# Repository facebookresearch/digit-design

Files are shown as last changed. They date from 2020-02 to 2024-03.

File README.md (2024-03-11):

# DIGIT-DESIGN


<a href="https://digit.ml/">
DIGIT-logo
</a>

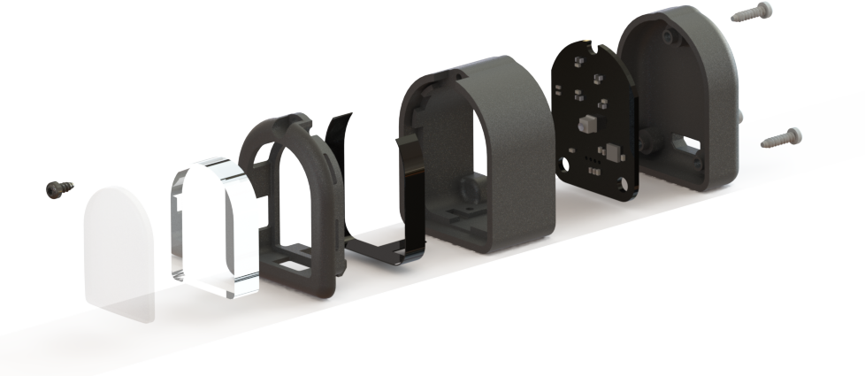
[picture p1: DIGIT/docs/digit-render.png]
DIGIT-render


Manufacturing design files for the [DIGIT tactile sensor](https://digit.ml).

**For updates and discussions please join the #DIGIT channel at the [www.touch-sensing.org](https://www.touch-sensing.org/) community.**

## Content

[This repository](DIGIT) contains the documentation and manufacturing files for the plastics enclosure, elastomer, electronics and the firmware binary.

## Design Notes

Due to some parts being out of stock due to shortages, we recommend the following part substituions:

* Digit Main PCB, Camera, OVM7692-RAAA with OVM7692-RYAA
* Digit Main PCB, MCU, FT900-R with FT900Q-C-T
* Digit Flex PCB, LEDs, ARGB1313HS-TR with 19-337C/RSBHGHC-A88/4T
    * Note: this change is only compatible with Digit Flex rev. 2021-2

## Quick Start

Manufacturing and assembly documentation is found in the [Quick Start Guide](/DIGIT/DIGIT_Quick_Start_Guide.pdf)

The manufacturing files are released in [releases](/DIGIT/releases) for PCBA fabrication.

## Questions and Contributing

If you have questions or need help with the content of this repo please open a ticket.
We welcome useful contributions to the repo -- if you want to contribute please read [how to contribute](CONTRIBUTING.md).

## License
These design files are licensed under CC-by-NC, as found in the [LICENSE](LICENSE) file.

## Citing
If you use this project in your research, please cite this [paper](https://arxiv.org/abs/2005.14679):

```BibTeX
@Article{Lambeta2020DIGIT,
  author  = {Lambeta, Mike and Chou, Po-Wei and Tian, Stephen and Yang, Brian and Maloon, Benjamin and Victoria Rose Most and Stroud, Dave and Santos, Raymond and Byagowi, Ahmad and Kammerer, Gregg and Jayaraman, Dinesh and Calandra, Roberto},
  title   = {{DIGIT}: A Novel Design for a Low-Cost Compact High-Resolution Tactile Sensor with Application to In-Hand Manipulation},
  journal = {IEEE Robotics and Automation Letters (RA-L)},
  year    = {2020},
  volume  = {5},
  number  = {3},
  pages   = {3838--3845},
  doi     = {10.1109/LRA.2020.2977257},
}
```
# DIGIT-PINKI-DESIGN



## Content

[This repository](DIGIT_Pinki) contains the documentation and manufacturing files for the plastics enclosure, elastomer, and assembly.

## Quick Start

Manufacturing and assembly documentation is found in the [Quick Start Guide](DIGIT_Pinki/DIGIT_Pinki_Quick_Start_Guide.pdf)

## Questions and Contributing

If you have questions or need help with the content of this repo please open a ticket.
We welcome useful contributions to the repo -- if you want to contribute please read [how to contribute](CONTRIBUTING.md).

## License
These design files are licensed under CC-by-NC, as found in the [LICENSE](LICENSE) file.

## Citing
If you use this project in your research, please cite this [paper](https://arxiv.org/abs/2403.05500).

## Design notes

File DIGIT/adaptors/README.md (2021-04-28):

DIGIT is designed to be natively compatible with the [Wonik's Allegro Hand](http://wiki.wonikrobotics.com/AllegroHandWiki/index.php/Allegro_Hand) 

In addition, we here provide files for 3d-printing adaptors for mounting DIGIT on several common robotic platforms:
- [Interbotix WidowX](https://www.trossenrobotics.com/widowxrobotarm)
- [Robotiq (2 and 3 fingers grippers)](https://robotiq.com/products)
- [Rethink Sawyer](https://www.rethinkrobotics.com/sawyer/)
- [Shunk](https://schunk.com/us_en/gripping-systems/category/gripping-systems/schunk-grippers/)
- [Weiss WSG Series](https://weiss-robotics.com/wsg-series/product/wsg-series/)

We welcome adaptors contributed from the community.

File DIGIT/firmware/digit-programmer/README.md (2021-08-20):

# DIGIT Programmer

A tool to allow flashing new firmware to the DIGIT device

This utility allows for downgrading or upgrading firmware, as well assigning a device serial number.

## Installation
Clone the repository and install the package using:

	git clone https://github.com/facebookresearch/digit-design.git
	cd digit-design/firmware/digit-programmer
	pip install -r requirements.txt

This tool also requires ```dfu-util```, install with:

    $ sudo apt install dfu-util

### Adding DIGIT and DIGIT-PROGRAM udev Rule
Add your user to the ```plugdev``` group,

    adduser username plugdev

Copy udev rule,

    sudo cp ./udev/50-DIGIT*.rules /lib/udev/rules.d/

Reload rules,

    sudo udevadm control --reload
    sudo udevadm trigger
    
Replug the DIGIT device into host.

### Firmware Download
The current public firmware release is found in the ```digit-design``` respository. 

## Usage
To upload firmware to the DIGIT device specify the path to the binary firmware file and the device's serial number (trailing zeros and D prefix is not required).

Default firmware binary file name is specified in ```programmer.yaml```.

Flashing DIGIT device with serial number ```D00045```,

    $ python3 flash.py digit.serial=45

Flashing DIGIT device with alternate firmware binary,

    $ python3 flash.py digit.firmware="digit-development.bin" digit.serial=45

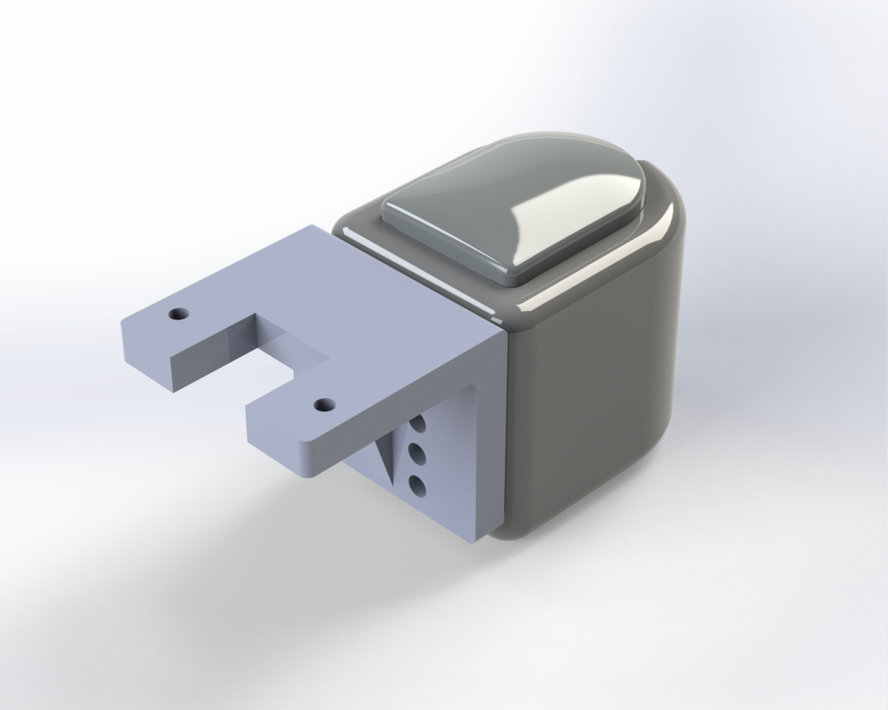
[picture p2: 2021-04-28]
DIGIT/adaptors/Interbotix/adaptor-interbotix.png

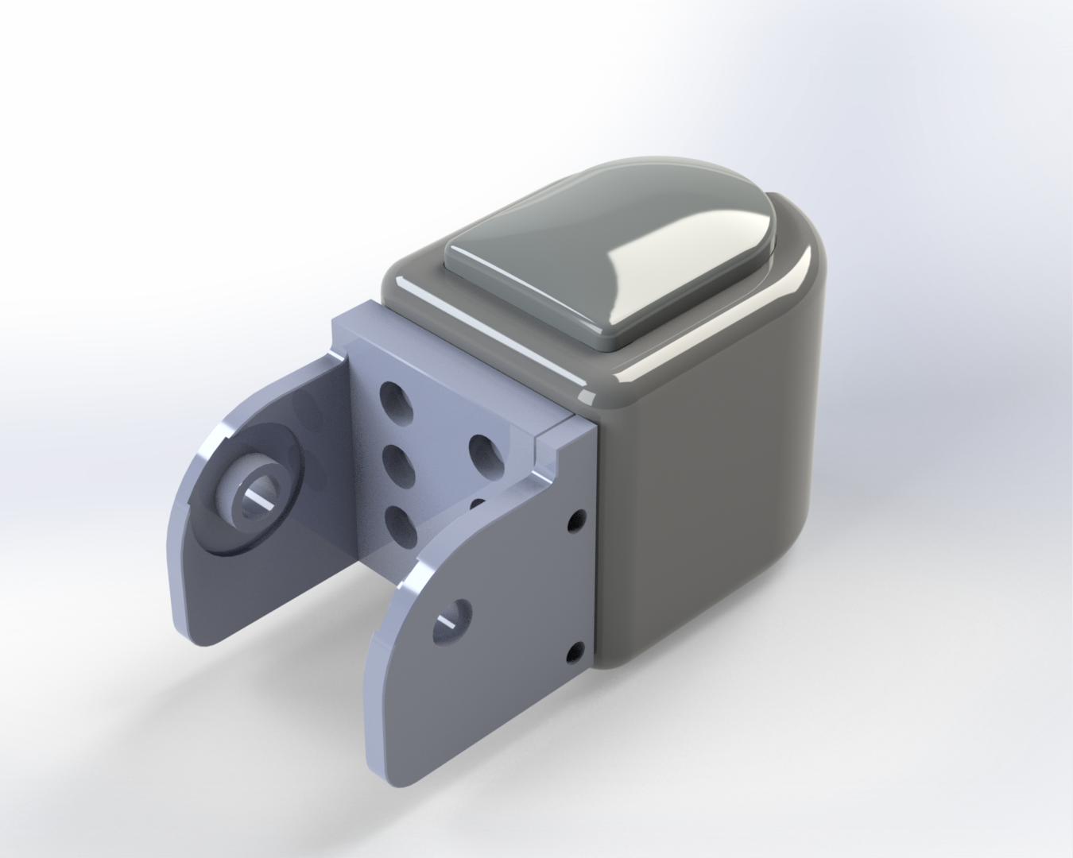
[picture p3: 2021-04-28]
DIGIT/adaptors/Allegro/adaptor-allegro.png

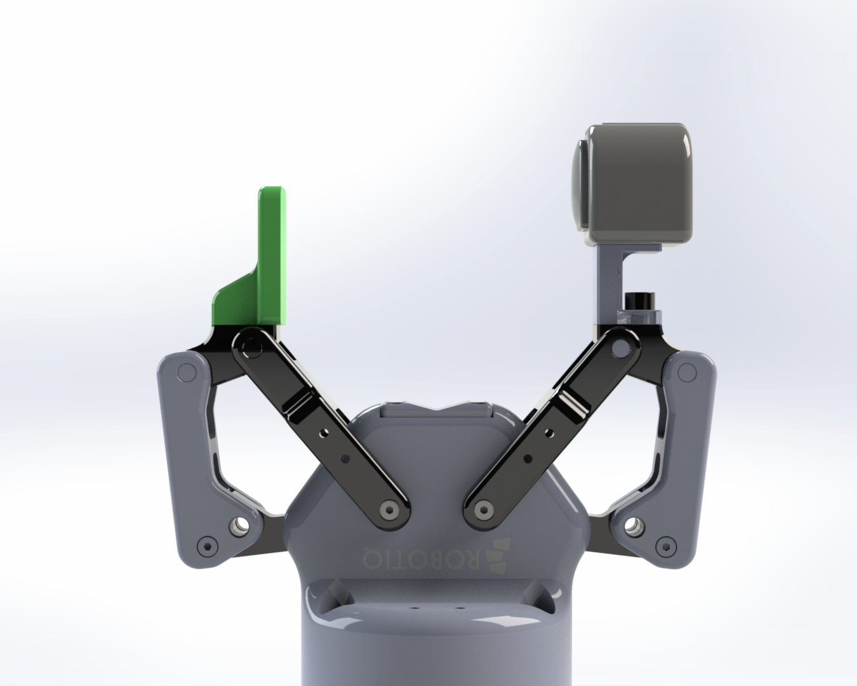
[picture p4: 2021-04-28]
DIGIT/adaptors/Robotiq/2F85/adaptor-robotiq-2f85.png

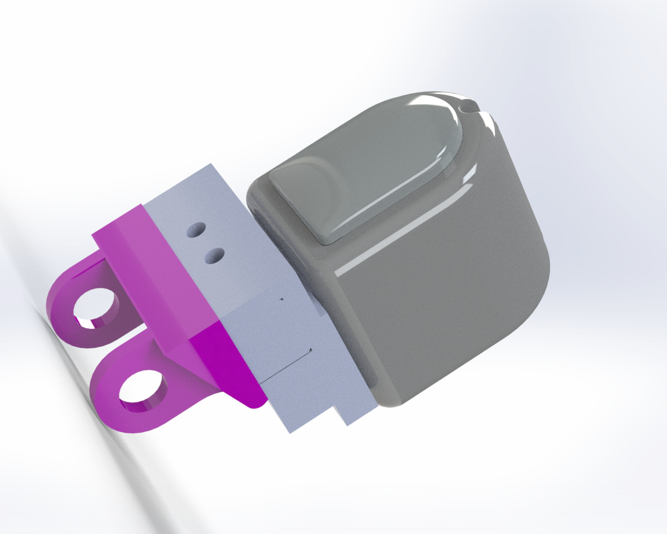
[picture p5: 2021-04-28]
DIGIT/adaptors/Robotiq/3-Finger/adaptor-robotiq-3-finger.png

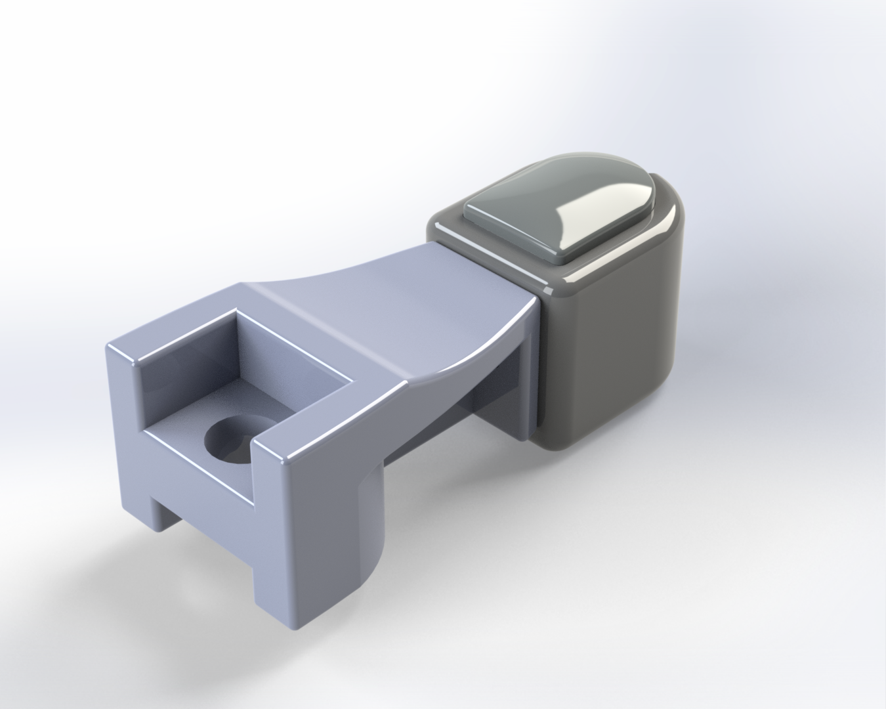
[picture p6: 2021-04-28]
DIGIT/adaptors/Schunk/adaptor-schunk.png

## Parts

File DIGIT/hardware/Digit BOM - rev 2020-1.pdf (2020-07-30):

Line # | Designator | Description | Qty. | Manufacturer | Manufacturer Part Number
1 | C1, C3, C4, C6, C7, C8, C10, C11, C12, C13, C17, C19, C21, C22, C23, C25, C26 | CAP 100nF 35V ±20% 0402 (1005 Metric) Thickness 0.6mm SMD | 17 | TDK | C1005X7R1V104M
2 | C2, C5 | CAP 10uF 6.3V ±20% 0402 (1005 Metric) Thickness 0.6mm SMD | 2 | TDK | C1005X5R0J106M050BC
3 | C9, C24 | CAP 4.7uF 10V ±10% 0603 (1608 Metric) Thickness 0.55mm SMD | 2 | KEMET | C0603C475K8PACTU
4 | C14, C15 | CAP 18pF 10V ±10% 0402 (1005 Metric) Thickness 0.6mm SMD | 2 | Vishay Vitramon | VJ0402A180KXQCW1BC
5 | C16, C18, C20, C27, C28, C29, C30 | CAP 1uF 6.3V ±10% 0402 (1005 Metric) Thickness 0.6mm SMD | 7 | Kyocera AVX | 04026D105KAT2A
6 J1 | | Micro USB Receptacle, Type B, SMT, Vertical, with Through-Hole Shell Stakes, -30 to 85 degC, 5-Pin SMD, RoHS, Tape and Reel | 1 | Global Connector Technology | USB3140-30-0230-1-C
7 L1, L2, L3 | | 3.3µH Shielded Multilayer Inductor 1.05A 250mOhm Max 0603 (1608 Metric) | 3 | Murata | LQM18PN3R3MGHD
8 P1 | | 16 Position Connector Receptacle, Center Strip Contacts Surface Mount Gold | 1 | Hirose | DF37NB-16DS-0.4V(51)
9 Q1, Q2 | | Dual General Purpose Transistors, NPN, 6-Pin SOT-563, Pb-Free, Tape and Reel | 2 | ON Semiconductor | BC847CDXV6T1G
10 | R1, R13, R14 | 1K 0.063W 5% 0402 (1005 Metric) SMD | 3 | Yageo | RC0402JR-071KL
11 R2, R3, R6 | | Chip Resistor, 10 KOhm, +/- 5%, 63 mW, -55 to 155 degC, 0402 (1005 Metric), RoHS, Tape and Reel | 3 | Rohm | MCR01MZPJ103
12 | R4, R5 | 12K 0.063W 1% 0402 (1005 Metric) SMD | 2 | Yageo | RC0402FR-0712KL
13 | R7 | 100R 0.063W 5% 0402 (1005 Metric) SMD | 1 | Vishay Dale | CRCW0402100RJNED
14 | R8, R10, R12 | 270R 0.063W 5% 0402 (1005 Metric) SMD | 3 | Panasonic | ERJ-2GEJ271X
15 | R9 | 82R 0.063W 5% 0402 (1005 Metric) SMD | 1 | Panasonic | ERJ-2GEJ820X
16 | R11 | 150R 0.063W 5% 0402 (1005 Metric) SMD | 1 | Vishay Dale | CRCW0402150RJNED
17 U1 | | FT900 Embedded Microcontroller, support both CAN Bus and Ethernet features, -40 to +85 degC, 100-Pin QFN, Pb-Free, Tape and Reel | 1 | FTDI | FT900Q-R
18 | U2 | CMOS with Processor Image Sensor 640H x 480V 1.75µm x 1.75µm | 1 | OmniVision Technologies | OVM7692-RAAA
19 | U3 | Linear Voltage Regulator IC 1 Output 300mA SOT-25 | 1 | Diodes Incorporated | AP7343-33W5-7
20 U4 | | Micropower 1.5V CMOS Voltage Regulator with Shutdown Control, 5-pin SOT-23, Pb-Free | 1 | TI National Semiconductor | LP3992IMFX-1.5/NOPB
21 X1 | | 12MHz ±25ppm Crystal 18pF 150 Ohms 4-SMD, No Lead | 1 | ECS International | ECS-120-18-36-AGM-TR
Line # | Designator | Description | Qty. | Manufacturer | Manufacturer Part Number
1 | D1, D2, D3, D4, D5 | LED RGB DIFFUSED SMD | 3 | Stanley Electric | ARGB1313HS-TR
2 | P1 | CONN HDR 16POS SMD GOLD | 1 | Hirose | DF37B-16DP-0.4V(53)

DIGIT Bill of Materials, Rev 2020-1

DIGIT Flex Bill of Materials, Rev 2020-1

Copyright (c) Facebook, Inc. and its affiliates. All rights reserved. This file is licensed under the license found in the LICENSE file in the root directory of this source tree.

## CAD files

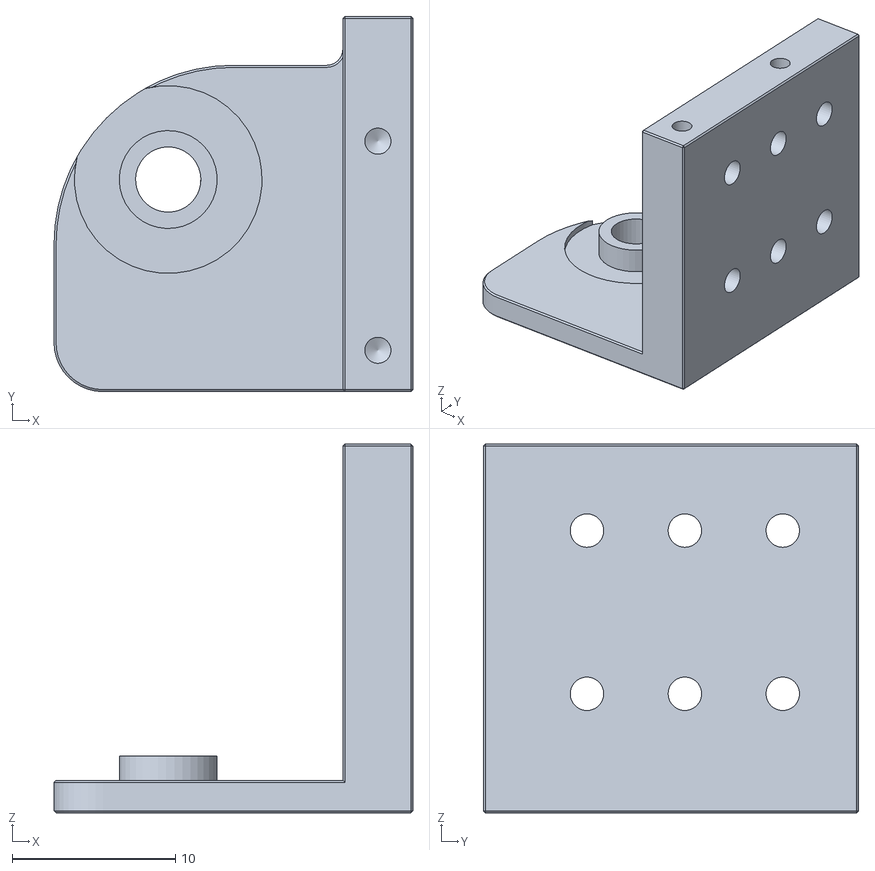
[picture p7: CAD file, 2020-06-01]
DIGIT/adaptors/Allegro/DIGIT-Allegro-main-V1.stl
22.0 x 23.0 x 22.6

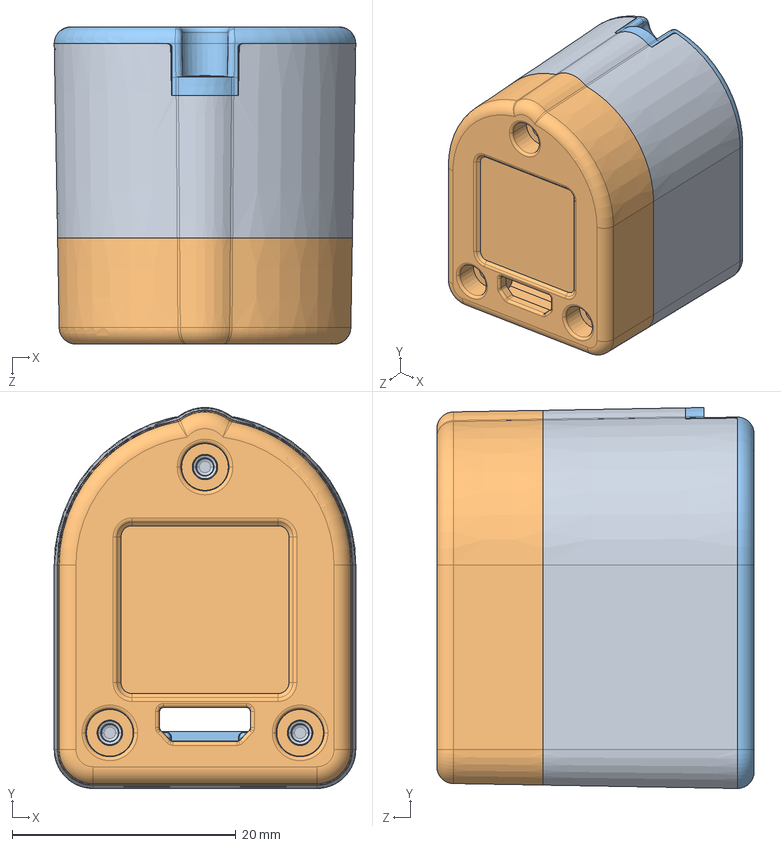
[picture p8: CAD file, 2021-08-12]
DIGIT/mechanical/EnclosureAssy_IM_Final.STEP
26.9 x 34.0 x 28.4 mm
CenterREDO_copy
BackREDO_copy
acrylicwindowREDO_rev2_copy

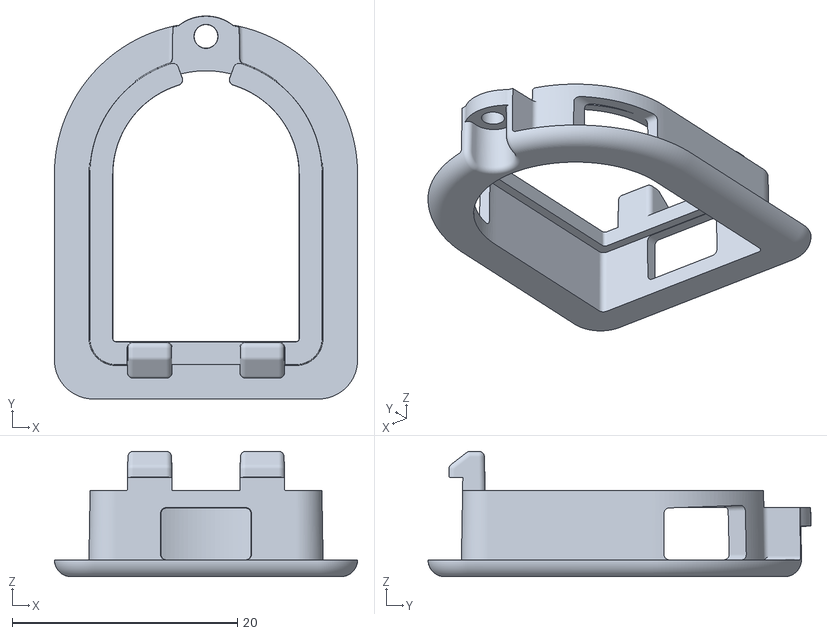
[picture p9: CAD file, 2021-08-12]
DIGIT/mechanical/EnclosureAssy_IM_Final_Window.STL
26.9 x 34.0 x 11.1

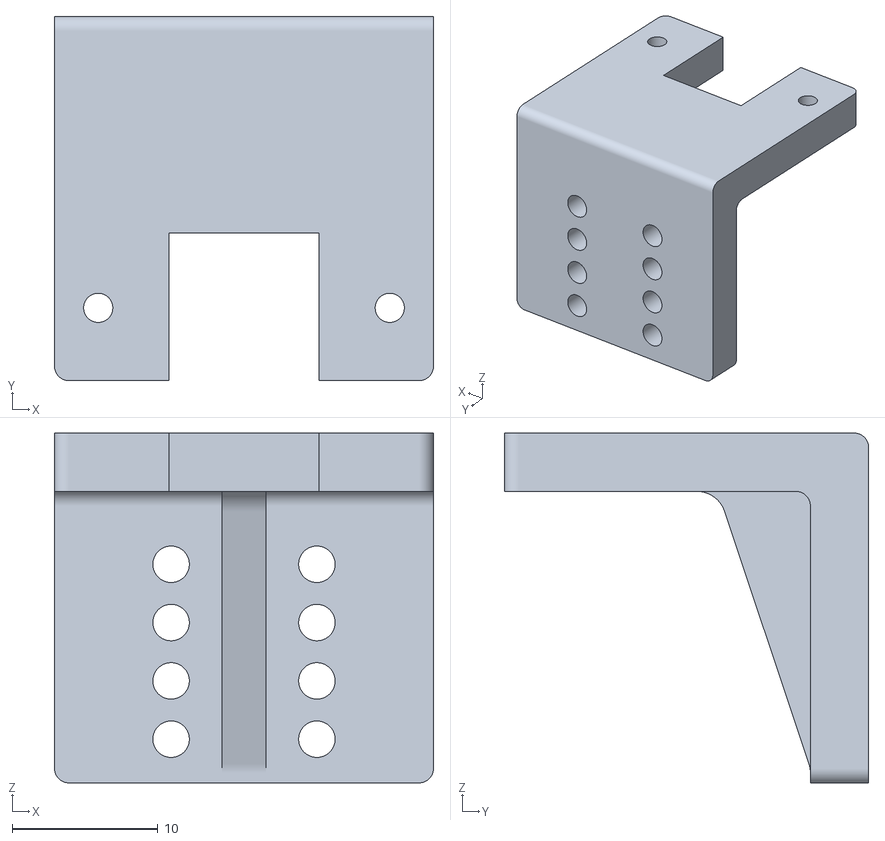
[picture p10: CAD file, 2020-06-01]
DIGIT/adaptors/Interbotix/DIGIT-WidowX-V1.STL
26.0 x 25.0 x 24.0

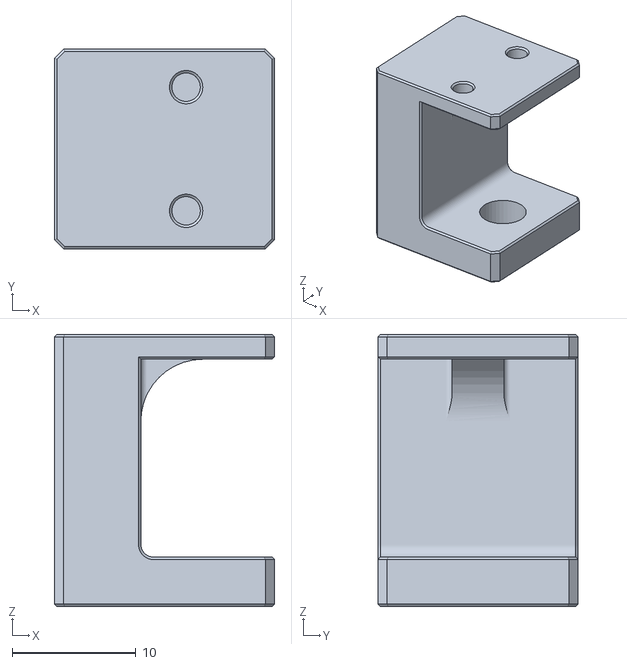
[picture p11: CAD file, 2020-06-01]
DIGIT/adaptors/Robotiq/2F85/DIGIT-Robotiq Adapter-2F85-V1.STL
17.8 x 16.2 x 22.0

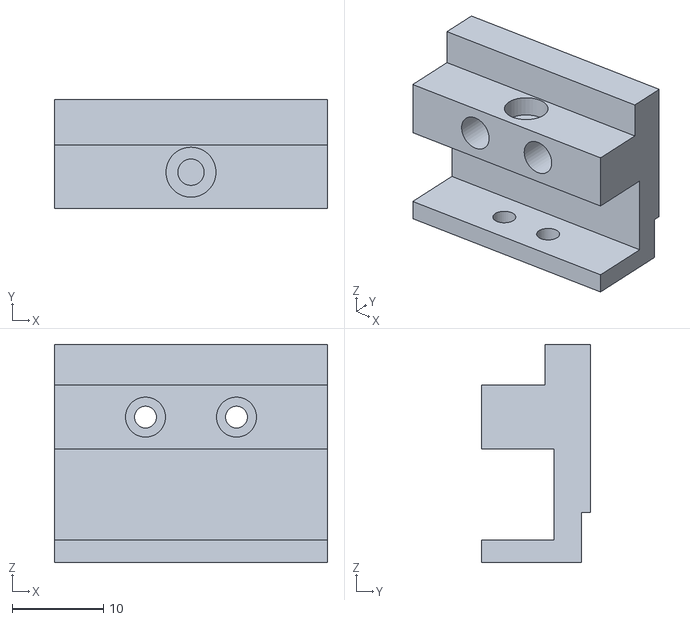
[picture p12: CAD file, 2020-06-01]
DIGIT/adaptors/Robotiq/3-Finger/DIGIT-robotiq-3fgr-bracket-V1.STL
30.0 x 12.0 x 24.0

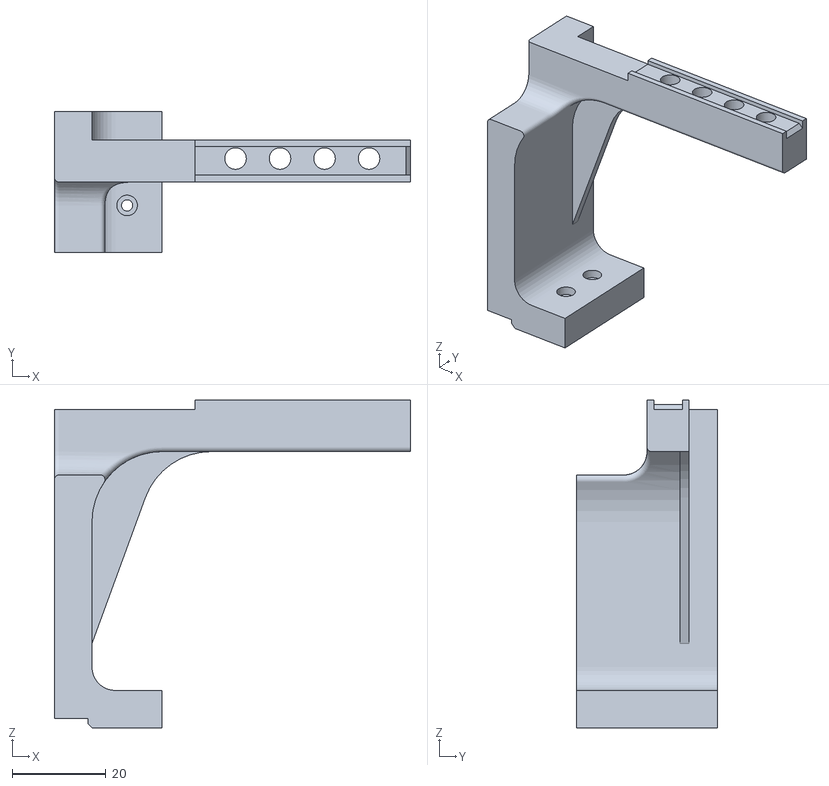
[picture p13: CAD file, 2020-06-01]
DIGIT/adaptors/Sawyer/DIGIT-Sawyer-V1.STL
76.0 x 30.0 x 70.0

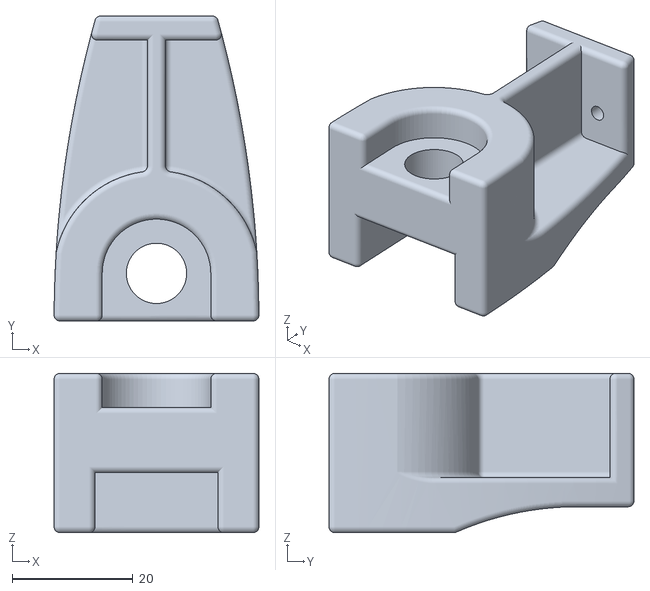
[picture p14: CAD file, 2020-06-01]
DIGIT/adaptors/Schunk/DIGIT-Schunk-V1.STL
34.0 x 50.6 x 26.5

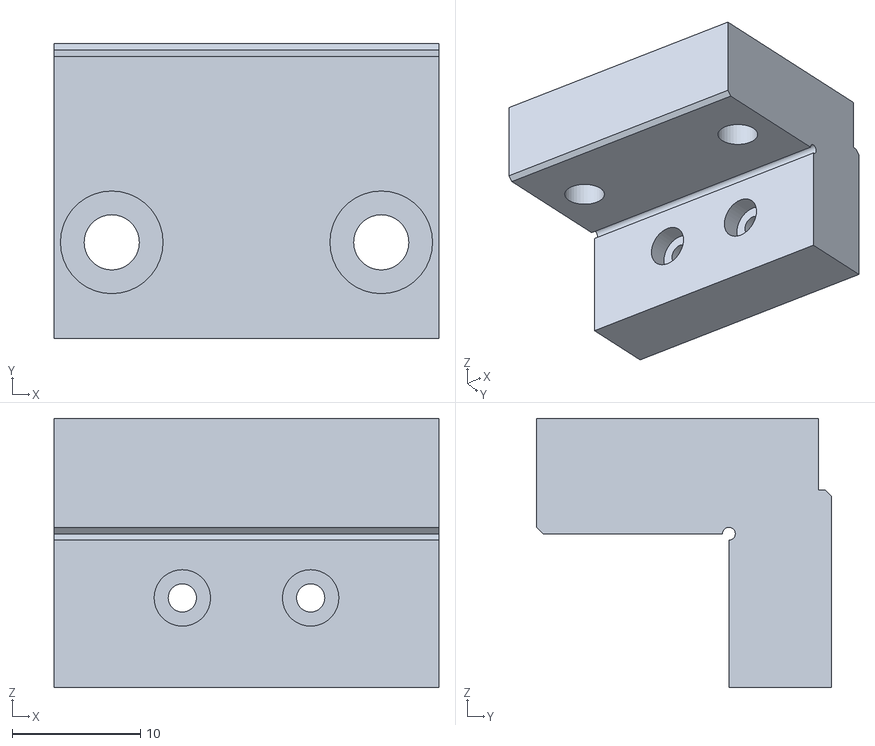
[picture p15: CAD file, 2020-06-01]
DIGIT/adaptors/Weiss/DIGIT-WSG-50-V1.STL
30.0 x 23.0 x 21.0

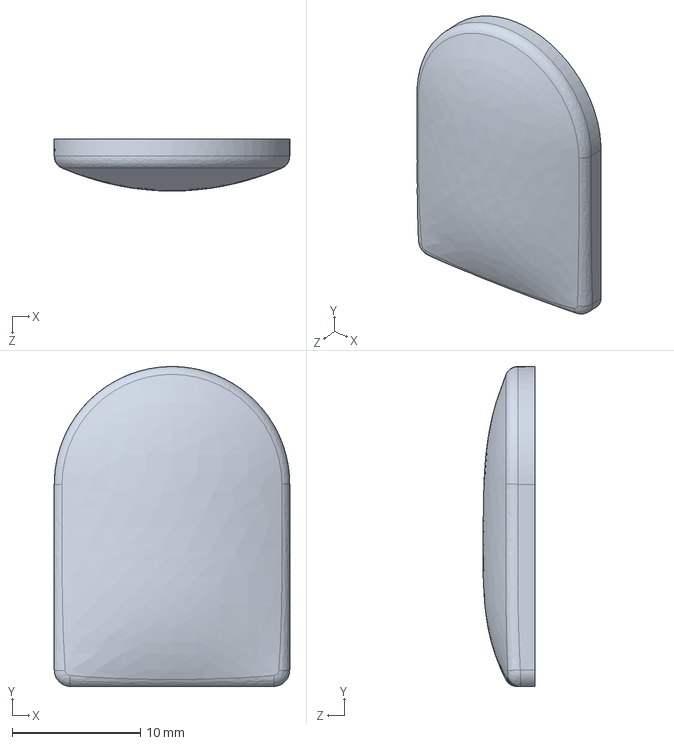
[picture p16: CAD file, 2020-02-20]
DIGIT/gel/Digit Gel.STEP
18.4 x 25.0 x 4.06 mm

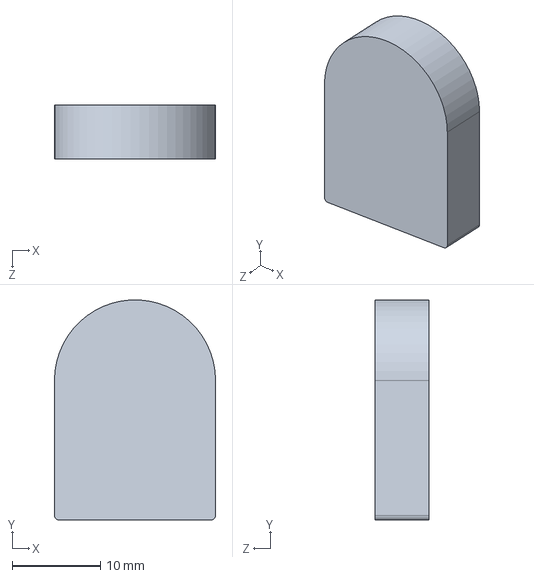
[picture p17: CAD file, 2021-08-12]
DIGIT/mechanical/Acrylic_Final.STEP
18.3 x 25.0 x 6.15 mm

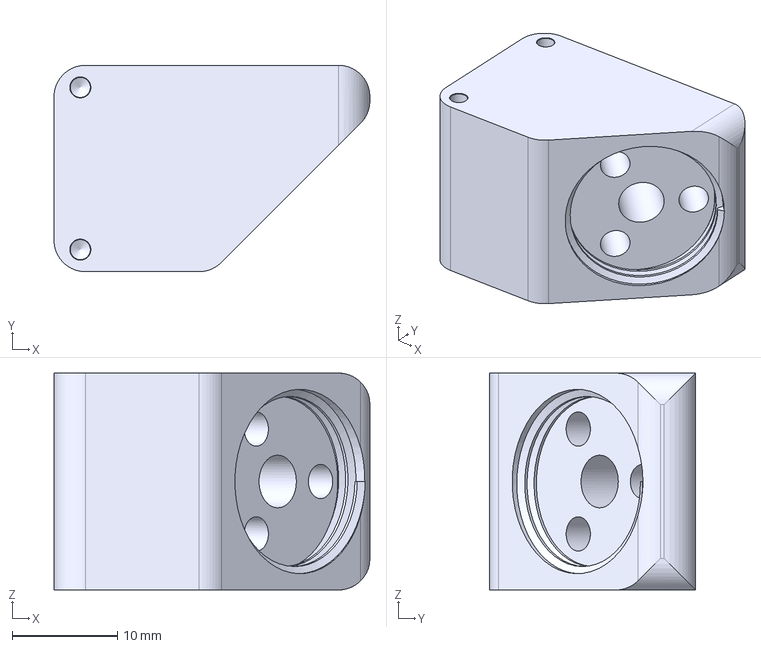
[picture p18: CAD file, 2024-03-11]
DIGIT_Pinki/adaptors/Allegro/AllegroHandAdaptor_3Fibers.step
30.0 x 19.6 x 20.6 mm

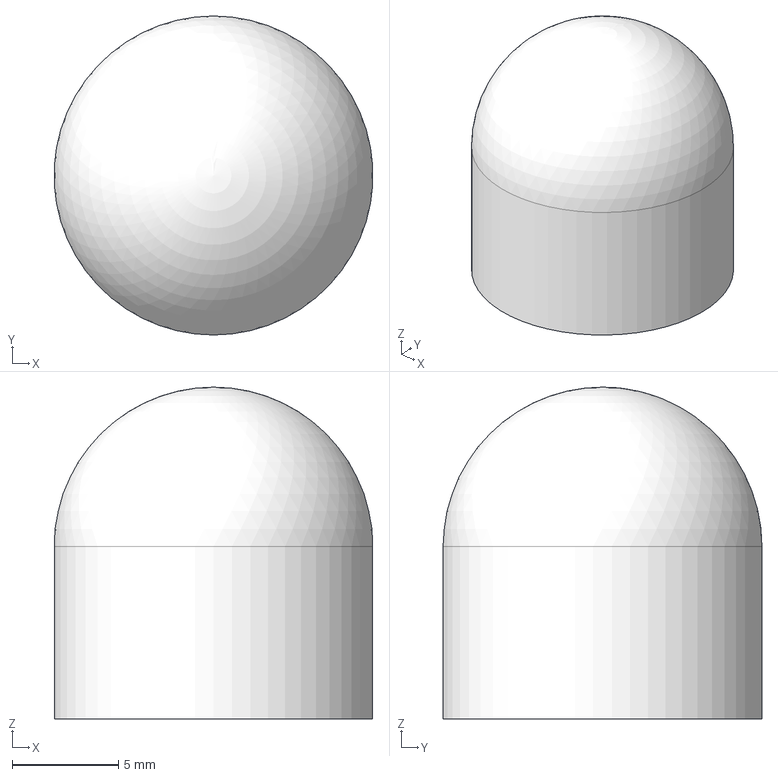
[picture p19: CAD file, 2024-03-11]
DIGIT_Pinki/gel/Pinki Gel.step
15.0 x 15.0 x 15.6 mm

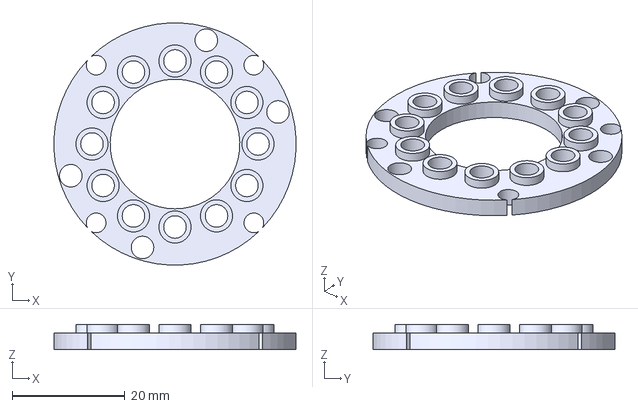
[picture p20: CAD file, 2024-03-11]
DIGIT_Pinki/mechanical/illumination/NeopixelLightGuideCollimator.step
42.9 x 42.9 x 4.50 mm

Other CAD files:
DIGIT_Pinki/mechanical/imaging/ArducamCageMount.step
DIGIT/adaptors/Allegro/DIGIT-Allegro-side-V1.stl
DIGIT/adaptors/Robotiq/3-Finger/DIGIT-robotiq-3fgr-base-V1.STL
DIGIT/mechanical/Label.DXF
DIGIT/mechanical/Acrylic_Final.DXF
DIGIT_Pinki/adaptors/Allegro/AllegroHandAdaptor_6Fibers.step
DIGIT_Pinki/adaptors/Allegro/AllegroHandAdaptor_9Fibers.step
DIGIT_Pinki/adaptors/Allegro/PinkiGelThread.step
DIGIT_Pinki/mechanical/illumination/NeopixelHolder.step
DIGIT_Pinki/mechanical/imaging/MicroscopeEyepieceCageMount.step

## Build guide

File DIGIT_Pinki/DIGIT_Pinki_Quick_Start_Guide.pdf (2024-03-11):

# DIGIT Pinki Quick Start Guide

# 1. Introduction

DIGIT Pinki is a compact, high-resolution tactile sensor suitable for operation in constrained spaces, such as medical palpation tasks. DIGIT Pinki uses optical fiber bundles to miniaturize the form factor of the sensing element significantly. This guide details the manufacturing, assembly, and quick start instructions for the DIGIT Pinki tactile sensor.

We recommend using the following printer settings for 3D-printed parts:

# 2. Distal Sensing Element Manufacturing

List of materials needed for making the elastomer gel and distal sensing element:

Part Number | Description | Quantity
1 | DIGIT Gel Mold | 1
2 | Vacuum degas chamber | 1
3 | Smooth-on Solaris Shore 10A | 1
4 | Smooth-on InhibitX | 1
5 | Smooth-on Ecoflex 00-10 | 1
6 | Smooth-on Silc-Pig White | 1
7 | Smooth-on NOVOCS Matte | 1
8 | Smooth-on Ease Release 200 | 1
Component | Specification
3D Printer | Stratasys J750
Layer Height | Default
Material | Vero Black Plus
Finish | Glossy

9 | Rustoleum Mirror Effect Spray | 1
10 | 99% Isopropyl Alcohol | 1
11 | Nitrile Glove | 2
12 | Cups | 2
13 | Wooden Mixing Sticks | 2
14 | Digital Scale | 1

To create the mold for the elastomer gel, one may either machine a metal mold or create a daughter mold. If you choose to machine the mold using the provided mold file (recommended), skip to Section 2.2. If you choose to create a daughter mold, go to Section 2.1.

## 2.1. Gel Daughter Mold

This section details how to create a daughter mold using silicone from a blank copy of the desired gel shape.

Materials needed in addition to the above material list:
- 1 pint unit of Mold Star 16
- 3D-printed or machined DIGIT Pinki gel shape
1. Clean the DIGIT Pinki gel shape with 99% isopropyl alcohol and place into a clean mold container, such as a cup or a box.
a. Use a silicone mold release on mold container if needed, letting outgas for 15-30 minutes after spraying.
b. Using mold release on the gel shape will create surface texture, so we recommend using a 3D-printed or machined gel shape.
2. Mix Mold Star 16 using 1:1 Part A to Part B by weight ratio, using the digital scale. After mixing well, pour mixture over the mold container until the Mold Star silicone fully encapsulates the gel shape.
3. Place in a vacuum degas chamber and vacuum 1 - 3 cycles at -85 kPA until there are no bubbles in the mold
4. De-mold the daughter mold from the container once Mold Star has cured after 4+ hours

## 2.2. Gel Base

This section details how to create the elastomer gel base once a mold (either machined or silicone) has been obtained.

Optional Materials:
- (Optional) Syringes with Luer Lock tip (recommended 14 Ga size or larger)
- (Optional) KimTech wipes
1. Clean the mold with 99% isopropyl alcohol and let the alcohol dry off.
2. (Only if you are using a silicone daughter mold) Spray the mold with silicone mold release, holding the mold release spray at least 6 inches away for an even coating.
a. Let outgas for 15-30 minutes
b. If there is too much excess mold release, repeat steps 1 and 2 again to avoid unnecessary surface texture.
3. Using a cup and wooden mixing stick, mix Solaris using 1:1 Part A to Part B by weight ratio.
4. Place the mixture in a vacuum degas chamber and vacuum for 1-3 cycles at -85kPA until there are no bubbles in the Solaris
5. Pour the Solaris mixture into the mold cavity.
a. (Optional) For more precision when putting the Solaris into the mold, use a syringe with a 14 Ga size or larger Luer Lock tip. Below is an image of Solaris injected into a silicone mold cavity.

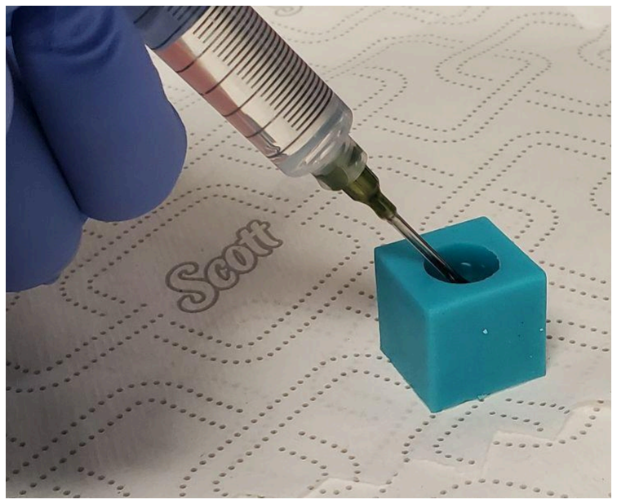
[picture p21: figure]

6. Place the filled mold into the vacuum degas chamber and again vacuum at 1-3 cycles at -85 kPA until there are no bubbles in the Solaris gel. This is to remove any bubbles that were introduced during the pouring process.
7. Let the Solaris cure for 24+ hours at room temperature and atmosphere pressure. We recommend covering the mold to prevent any dust
8. Demold the gel from the mold.

## 2.3. Gel White Paint Mixture

Next, prepare the white silicone paint mixture that will coat the finished gel surface.

1. Mix Smooth-on Ecoflex 00-10 evenly with equal parts A and B.
2. Add in 3% white Silc Pig pigment by weight.
3. Dilute the white Ecoflex 0010 with NOVOCS matte 0.8% by weight. The result should have a similar consistency to liquid yogurt. You may test out the mixture and add more or less NOVOCS matte as suitable.
4. Set aside the resulting white silicone paint mixture for the final assembly step.

## 2.4. Gel Surface Layer Assembly

This section details how to create the surface layers on top of the optically-clear base gel.

Optional Materials:
- (Optional) Airbrush system
- (Optional) heat gun
- (Optional) Latex-free cosmetic blender wedge
1. Clean surface of the Solaris gel with 99% isopropyl alcohol

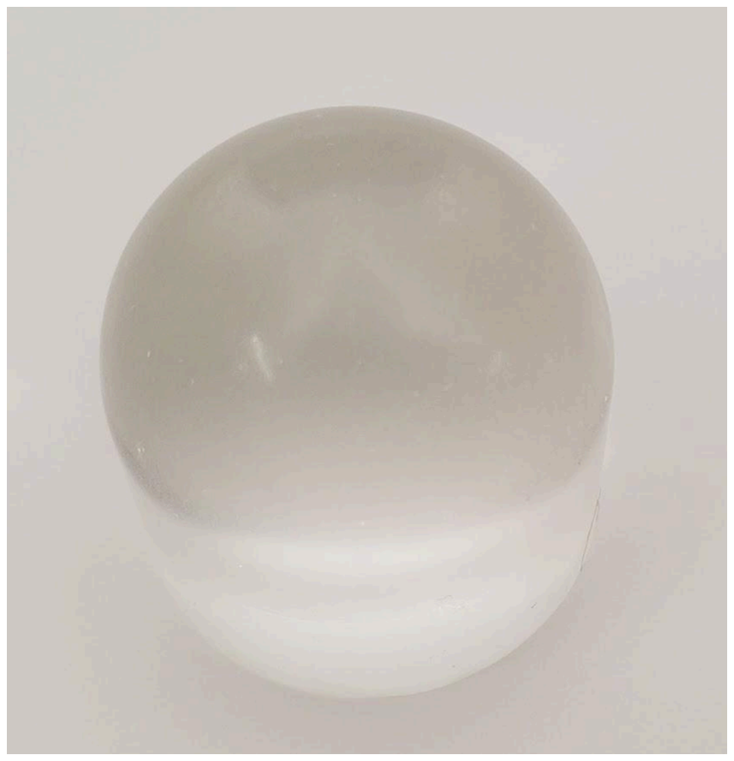
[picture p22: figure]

2. Coat the gel with a thin layer of InhibitX (may be airbrushed if desired).
a. Let outgas for 15 - 30 minutes.
3. Using Rustoleum Mirror Effect, spray the gel with 3-5 horizontal passes across the entire surface until there is an even silver coating.
a. Let dry for 15 - 30 minutes.
4. Apply another thin (may be airbrushed) layer of InhibitX
a. Let outgas for 15 - 30 minutes
5. Using a thin wooden mixing stick, thinly drip coat the surface of gel with the white paint silicone mixture. The mixture should drip down like coating a candy surface.

a. (Optional) Use a Latex-free cosmetic foam blender wedge or a syringe to evenly distribute the white silicone if dripping is not sufficient
b. Set aside in a covered (dust-free) environment to cure for 4 hours or set using heat gun if time sensitive.

## 2.5. Sensing Element Assembly

With a completed hemispherical gel (with the reflective layer and protective white paint layer), we may then assemble it into the mechanical enclosure.

Part Number | Description | Quantity
1 | 3D-printed thread | 1
2 | 3D-printed housing enclosure | 1
3 | Cyanoacrylate | 1
4 | Cargille Optical Gel | 1
1. Using cyanoacrylate, adhere the 3D-printed thread to the base of the gel so that the gel may be screwed onto the housing enclosure.
2. Use the index-matched Cargille optical gel on the base of the gel before screwing it on.

# 3. Illumination System Fiber Assembly

In this section, we detail how to assemble the illumination fiber bundle.

Part Number | Description | Quantity
1 | PMMA Fibers (e.g. 265μm with 48 Fiber Light Guide) | 1
2 | Razor blade or cutting knife | 1
3 | Sandpaper (180, 400, 1000 grit) | 1
4 | 99% Isopropyl Alcohol | 1
5 | Cyanoacrylate (super glue) | 1

6 | Sil-Poxy | 1
7 | Neopixel Ring | 1
8 | 3D-printed Neopixel Enclosure | 1
1. Cleave fiber ends using a razor blade. If possible, use a fiber cutting block or other similar jig in order to ensure a blunt, perpendicular face
2. Polish and clean fiber ends:
a. Use 180 grit (dry), 400 grit, and then 1000 grit (wet) sandpaper. Sand in a “Figure 8” motion for 20 passes with each sandpaper.
b. Clean the end faces with 99% isopropyl alcohol after sanding.
3. Bundle the fibers into the fiber mount.
4. Press fit the fiber bundle into fiber mount and use sharp scissors or shears to trim to edge.
a. Securely adhere using one drop of cyanoacrylate.
5. Adhere mount to elastomer gel through the enclosure conduits using Sil-Poxy
a. Do not move until Sil-Poxy has cured or else the mount will delaminate
6. On the illumination side, adhere fibers to LEDs using cyanoacrylate

# 4. Imaging Optical Bench Setup

In this section we describe the setup used for magnifying and imaging the output from the coherent fiber bundle.

List of materials needed:

Part Number | Description | Quantity
1 | Coherent Imaging Fiber Bundle with Adjustable Diopter | 1
2 | 16MP IMX298 USB camera | 1
3 | 10x plan Microscope objective | 1
4 | Microscope Eyepiece | 1
5 | ThorLabs Optical Metric Breadboard | 1
6 | ThorLabs Cage Plate Mounting Base for 30 mm Cage | 1

6 | ThorLabs 30 mm C-Mount-Threaded 30 mm Cage Plate | 1
7 | 3D-Printed Custom Cage Mount for Microscope Eyepiece | 1
8 | 3D-Printed Custom Cage Mount for Arducam | `1
9 | ThorLabs 30 mm Cage System Cover | 1
10 | ThorLabs 6 Inch Optical Cage Rods | 1
11 | 99% Isopropyl Alcohol | 1
12 | KimTech Wipes | 2
13 | M6 Screws | 4
14 | M4 Screws | 2
15 | (Optional) ThorLabs Cage Alignment Guide | 1
1. Assemble the optical cage and optical relays:
a. Align the 10x plan microscope objective and microscope eyepiece to the breadboard by screwing them into the C-mount cage plate and the custom 3D-printed cage plate, respectively.
b. Secure both to the optical cage to the breadboard using the metric screws
c. Attach the rods
d. Remove any dust using the KimTech wipes and 99% Isopropyl Alcohol.
2. (Optional) Verify alignment visually using the ThorLabs Cage Alignment Guide
3. Then align the USB camera to one end of the optical relays, and the coherent fiber bundle to the other end of the optical relays.
4. To verify the system, plug in the USB camera to your computer and verify that you can see the fibers clearly.
a. If the image is out of focus, manually focus the lens on the USB camera or the adjustable diopter.

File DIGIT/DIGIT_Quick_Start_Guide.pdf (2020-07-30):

# Quick Start Guide

[ 06 June 2020 ]

## 1 Introduction

DIGIT [1], is an inexpensive, compact, and high-resolution tactile sensor geared towards in-hand manipulation. DIGIT improves upon past vision-based tactile sensors by miniaturizing the form factor to be mountable on multi-fingered hands, and by providing several design improvements that result in an easier, more repeatable manufacturing process, and enhanced reliability. To provide the robotic community access to reliable and low-cost tactile sensors, we open-source the DIGIT design at www.digit.ml.
This white paper aims to provide manufacturing, assembly and quick start instructions for the DIGIT tactile sensor.

## 2 Repositories

There are two main repositories which contain the open-sourced sensor design, and a Python library for interfacing with the DIGIT sensor.
https://github.com/facebookresearch/digit-design
https://github.com/facebookresearch/digit-interface

1

## 3 Required Materials

### 3.1 Components List

DIGIT assembly requires the following tools and off-the-shelf components:

Part No. | Description | Quantity
1 | 1.5 mm Metric Hex Driver | 1
2 | Hex Socket Screw M2 x 0.4 mm Thread, 5 mm Long | 3
3 | Hex Socket Screw M2 x 0.4 mm Thread, 3 mm Long | 1

The following components compose the DIGIT main electrical and mechanical design, which are manufactured through internal or external vendors.

Part No. | Description | Quantity
1 | DIGIT Printed Circuit Board (PCB) | 1
2 | DIGIT Lighting PCB | 1
3 | DIGIT Rear Housing | 1
4 | DIGIT Main Housing | 1
5 | DIGIT Acrylic Clip Housing | 1
6 | Acrylic Window | 1
7 | Gel | 1

2

## 4 Manufacturing Recommendations

### 4.1 Electrical

Two components are required which can be manufactured via a turnkey printed circuit board assembly service, or by hand populating manufactured PCBs.

- Main PCB containing camera system
- Lighting flex PCB

The Gerber design files are found within the digit-design repository and are manufactured with the following specifications:

Specification
Layer Count | 4
Material | 370HR or FR4
Min Track/Spacing | 4mil/4mil
Thickness | 1.6mm
Solder Mask | Black
Silk Screen | Top and Bottom
Silk Screen Color | White
Surface Finish | ENIG
Via Process | Tented Via
Finished Copper | 1 oz.
(a) Main PCB specifications

Specification
Layer Count | 2
Material | Polymide Flex
Min Track/Spacing | 3mil/3mil
Thickness | 0.23mm
Solder Mask | Black
Silk Screen | Top
Silk Screen Color | White
Surface Finish | ENIG
Via Process | Tented Via
Finished Copper | 1.5 oz.
(b) Flex PCB specifications

The PCB stackup for the 4 layer main PCB board is as follows,

- Top Layer - digit copper signal top.gtl
- Internal Layer 1 - digit copper signal 1.g1
- Internal Layer 2 - digit copper signal 2.g2
- Bottom Layer - digit copper signal bot.gbl

3

### 4.2 Mechanical

The DIGIT mechanical body consists of three 3D-printed parts and one laser cut part. The 3D printed parts are the main, back, and acrylic clip housings shown in figure 1.

(a) Rear | (b) Main | (c) Acrylic Holder

Figure 1: Mechanical housing components

We recommend using the following 3D printer specifications,

Specification
3D Printer | Stratasys J750
Layer Height | Default
Material | Vero Black Plus
Finish | Glossy

Additionally, the gel acrylic window is laser cut from a sheet of 4 mm thick optically clear acrylic.

4

## 5 Assembly

Upon manufacturing both the mechanical and electrical parts, DIGIT can be assembled within 5 minutes.

Step 1

Press fit the DIGIT PCB into the back housing as shown in figure.x.

Figure 2: PCB inserted into back housing

Step 2

Bend the flex PCB connector 90 degrees and insert the DIGIT flex PCB into the perimeter of the main housing as shown in Figure 3.

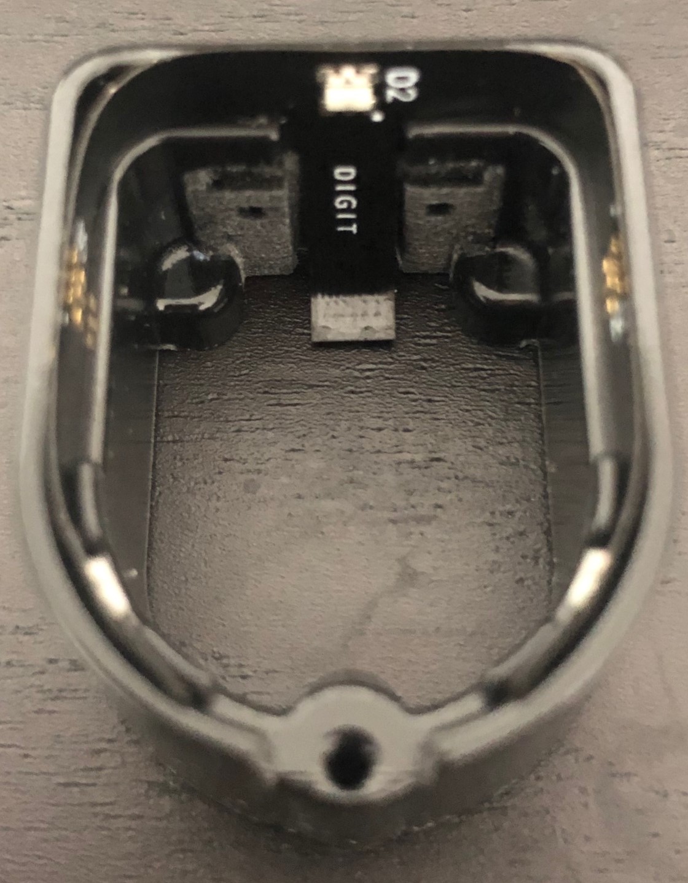
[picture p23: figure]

Figure 3: Flex PCB inserted into main housing

5

Step 3

Press fit the back and main housings together,

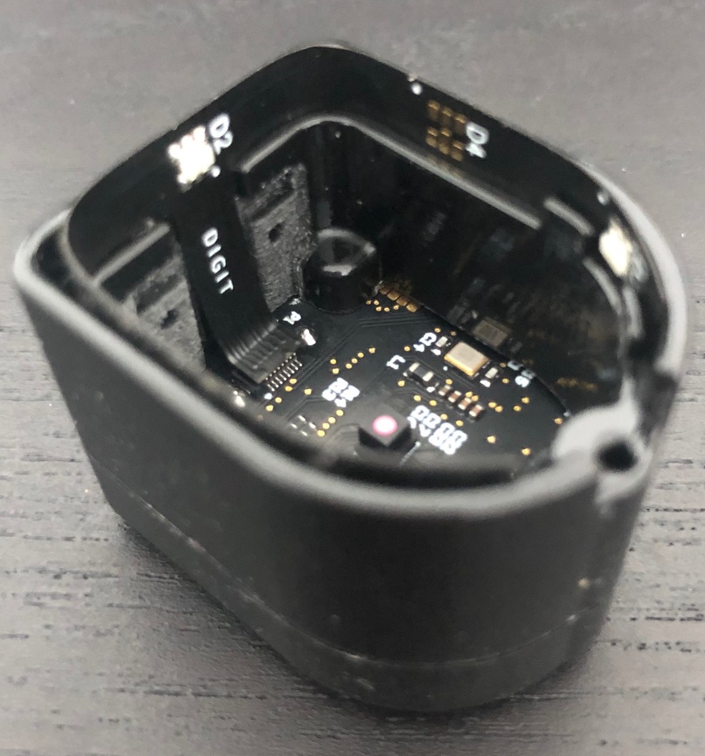
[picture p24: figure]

Figure 4: Back and main housing coupled together

Using your finger connect the flex PCB to the main PCB with a firm push, you should feel the connector snapping into place.

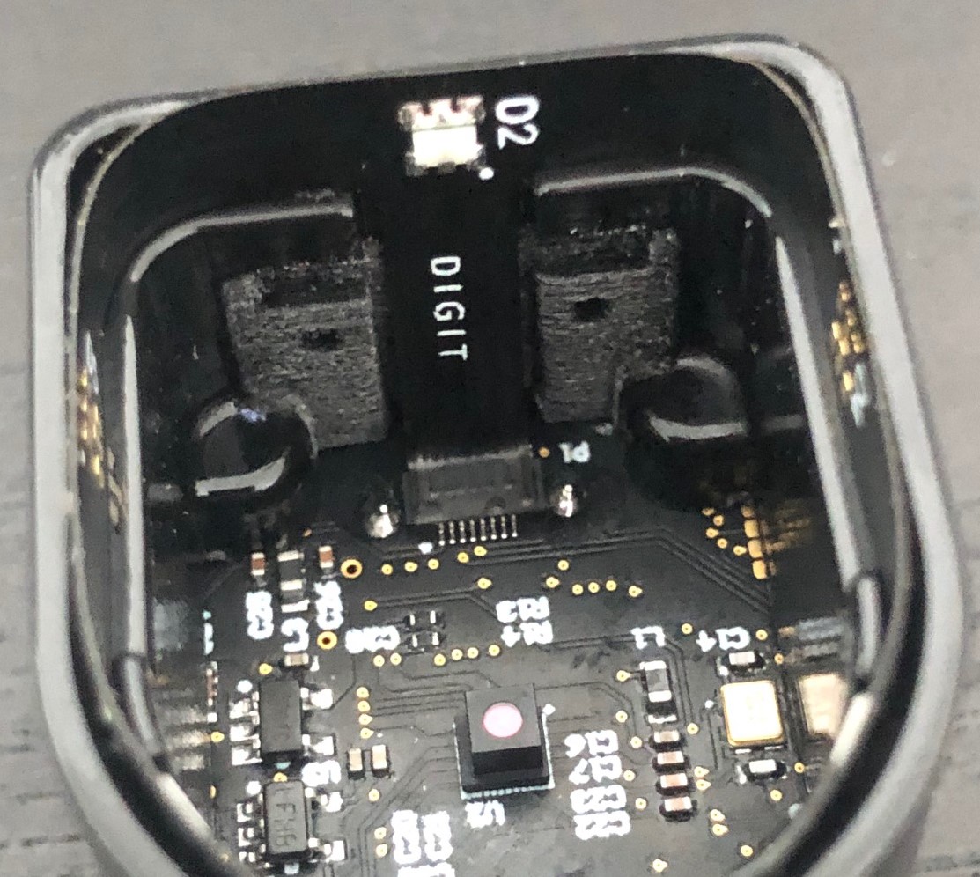
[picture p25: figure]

Figure 5: Flex PCB connected to main PCB

Step 4

Insert the gel into the acrylic holder housing,

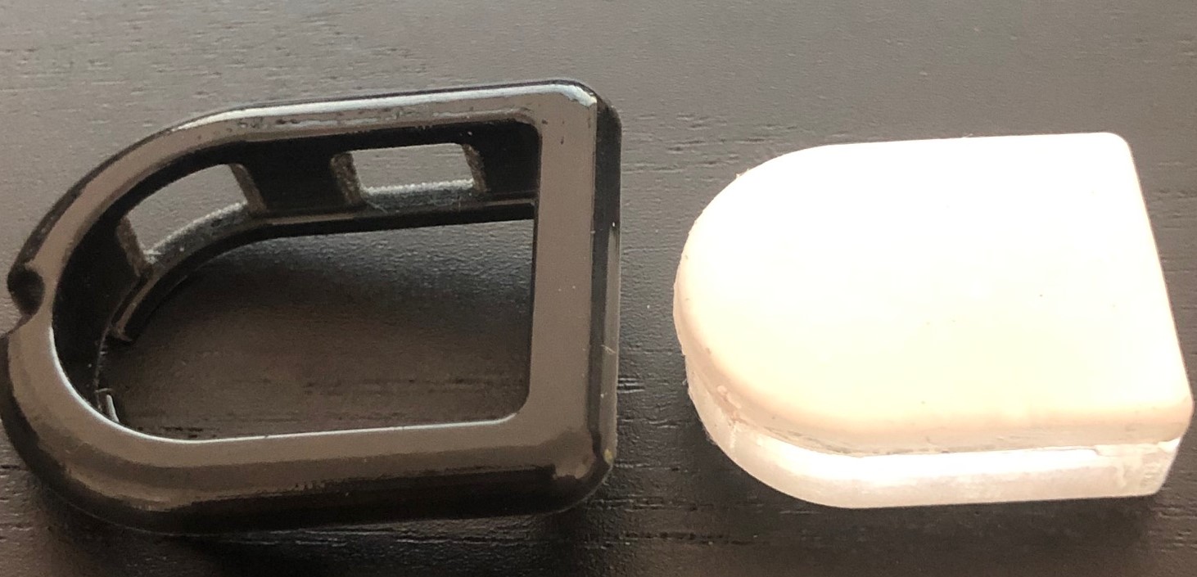
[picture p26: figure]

Figure 6: Gel and acrylic holder housing

Following this, snap fit the acrylic holder to the main housing,

6

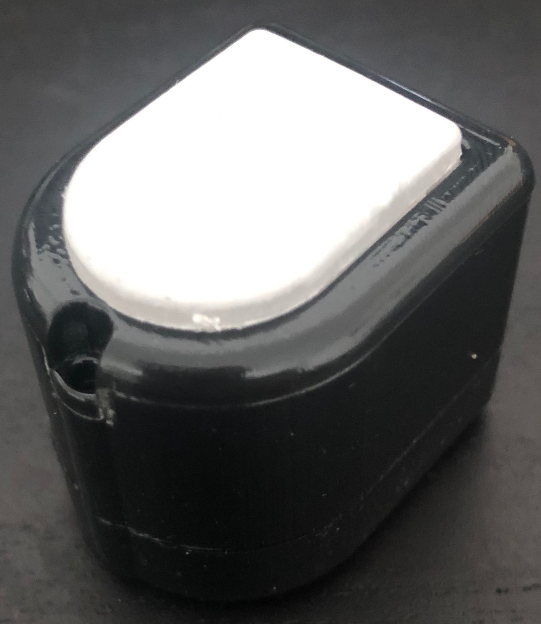
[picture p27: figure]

Figure 7: Main housing with acrylic housing

Step 5

Insert and fasten the three 5 mm hex screws into the back housing,

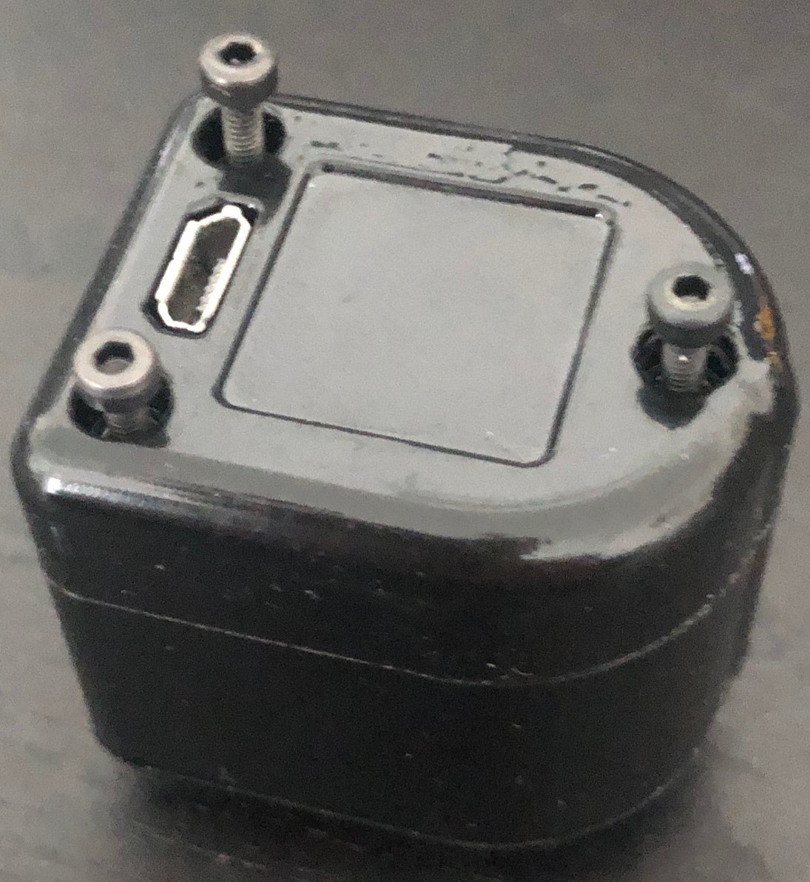
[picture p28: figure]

Figure 8: Back housing with inserted screws

Insert and fasten one 3mm hex screw into the acrylic housing,

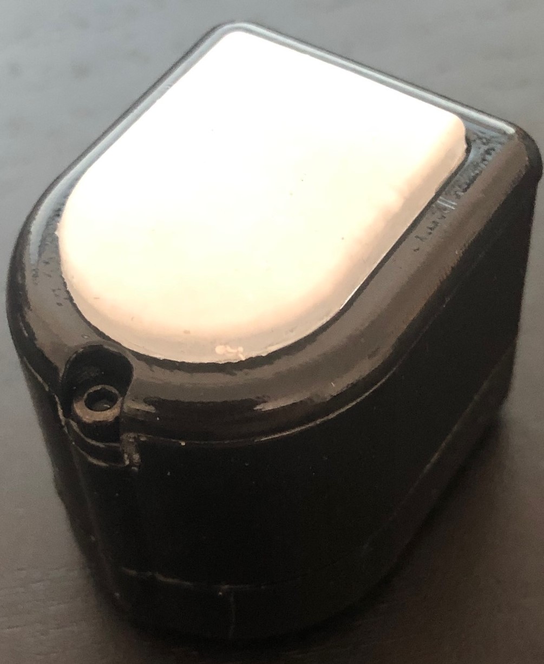
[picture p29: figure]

Figure 9: Acrylic housing with inserted screw

7

## 6 Gel Manufacturing

The DIGIT design repository contains the 3D files for the gel mold. This mold can either be produced via subtractive or additive manufacturing. The DIGIT gel mold consists of a 3x3 array of gels, it is best recommended to machine this mold out of aluminum. If manufacturing by 3D printing, sand each gel well in post to remove any layer lines.
It is recommended to start out with a small batch until all mixtures and results achieve the desired results for the end application. Following this, a large set of DIGIT gels can be produced by increase the number of molds and running larger batches.
The following tools, parts and chemicals are required for the manufacture of DIGIT gels.
Part No. | Description | Quantity
1 | DIGIT Gel Mold (gel/Digit Gel Mold.stp) | 1
2 | 2 x Airbrush Systems or 1 System with 2 Heads | 1
3 | Heat Source (Heat Gun or Blowdryer) | 1
4 | Smooth-On Solaris Shore 10A | 1
5 | Smooth-On Inhibit X | 1
6 | Smooth-On EcoFlex 00-10 | 1
7 | Smooth-On White Silicone Pigment | 1
8 | Smooth-On Sil-Poxy Optically Clear Adhesive | 1
9 | Smooth-On NOVOCS Matte | 1
10 | 99% Isopropyl Alcohol | 1

### 6.1 Preparing White Paint Mixture

Step 1

Mix an equal part A/B solution of EcoFlex 00-10.

Step 2

Add the white silicone pigment such that it is 3% of the total weight of the previous mixture.

Step 3

Thin out the mixture to 20% of the total weight using NOVACS and mix well until smooth. You may test out the mixture by observing how well the it is applied via the airbrush. Increase the amount of NOVACS until a uniform stream of white paint is expelled from the airbrush against a surface.

8

### 6.2 Manufacturing the DIGIT Gel

Step 1

Clean the molds thoroughly with 99% isopropyl alcohol and let dry.

Step 2

Apply Solaris 10A silicone into the molds and let cure on a flat surface, and inside a contained space with no turbulent air movement.

Step 3

Remove the gels from the mold and clean with 99% isopropyl alcohol.

Step 4

Arrange the gels on a flat plastic (sheet of acrylic) surface with the curved surfaces facing upwards.

Step 5

Setup one airbrush with Smooth-On Inhibit-X and apply a layer evenly across all the gels.

Step 6

Within 30 minutes of Step 5, prepare the second airbrush with the white paint mixture. Spray an even coating across the gels.

Step 7

After spraying the white paint onto the gels, use a heat source to quickly cure the first layer and then repeat Step 6 and Step 7 once more for a total of 2 layers. The amount of paint layers applied determines the spatial resolution transfer of objects touching the gel surface. This may be repeated once more for a total of 3 coats, or more depending on the application needs of the sensor.

Step 8

Let fully dry in an enclosed area to prevent any dust from adhering to the surface of the white paint layers.

9

Step 9

Apply the gel using an optically clear adhesive to the acrylic window and set to dry. It is best to apply a pea sized amount to the center of the acrylic window and depress the gel squeezing out any excess adhesive. Remove excess adhesive with a foam swap or by wiping away.

10

## 7 Flashing Firmware

The DIGIT sensor can be programmed with any DFU flashing utility. We have provided such utility inside the digit-design repository.
Upon manufacturing your DIGIT, connect the device to a host computer. The sensor should enumerate in DFU mode.
Flash the firmware with a unique integer only serial number.
1 | $ python3 flash.py digit.serial=45
| When finished flashing, cycle the power on the device by removing and re- inserting the USB cable to the host computer. The sensor will first enumerate in DFU mode for 3 seconds and then re-enumerate as a DIGIT device.

## 8 Quick Start Example

| Install the digit-interface Python package (https://github.com/facebookresearch/digit-interface) and connect the DIGIT sensor to a host computer using a Micro USB cable and specify the DIGIT serial number. Record the serial number which is either located on the sensor label, or specified through the programming tool. The following example can be used to connect to a DIGIT and acquire live sensor output, additional examples are located in the digit-interface repository.
1 | from digit_interface.digit import Digit
2 | from digit_interface.digit_handler import DigitHandler

3
4 | # Change D12345 to your DIGIT serial number,
5 | # and specify a friendly name
6 | digit = Digit("D12345", | "Left Gripper")
7 | digit.connect()

8
9 | # Print device info
10 | print(digit.info())

11
12 | # Display stream obtained from DIGIT
13 | digit.show_view()

14
15 | # Disconnect DIGIT stream
16 | digit.disconnect()

11

## References

[1] Mike Lambeta, Po-Wei Chou, Stephen Tian, Brian Yang, Benjamin Maloon, Victoria Rose Most, Dave Stroud, Raymond Santos, Ahmad Byagowi, Gregg Kammerer, Dinesh Jayaraman, and Roberto Calandra. DIGIT: A novel design for a low-cost compact high-resolution tactile sensor with application to in-hand manipulation. IEEE Robotics and Automation Letters (RA-L), 5(3):3838–3845, 2020.

12

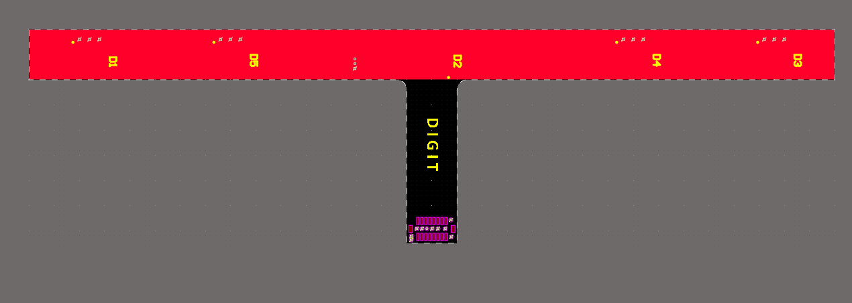
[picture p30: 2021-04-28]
DIGIT/hardware/fabrication/digit-flex/2021-2/Adhesive Outline.PNG

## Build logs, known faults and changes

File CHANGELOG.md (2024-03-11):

# Changelog

## 2024-03-10
- Added DIGIT Pinki manufacturing and assembly
- Refactored folder structure

## 2021-08-12

- Updated mechanical revision to address rasied issues

## 2021-06-28

- Release revision 2021-2 for Digit Flex
    - Changed LED (D1-D5) part number to 19-337C/RSBHGHC-A88/4T

## 2021-04-27

- Released beta firmware (2.00) to support individual RGB control of LED's

## 2020-10-19

- Added assembly view information for DIGIT main and lighting flex PCB
- Added adhesive outline for light flex PCB directly into mechanical layer 2 reflected in gerber files

## 2020-07-30

- Updated DIGIT firmware from 1a to 1b, fixed dfu-util programming issue

## 2020-06-06

- Added fabrication release with BOM, GerberX2, XY files and assembly info for fabrication houses
- Added SMT XY files for Pick and Place
- Updated Gerbers to GerberX2, fixed 2020-1 pick and place assembly DIGIT gerbers
- Updated descriptions in BOM, does not affect design.
- Improved digit-programmer README

## 2020-06-05

- Updated Quick Start Guide with gel manufacturing information

## 2020-06-03

- Improved README
- Improved how to contribute

## 2020-06-01

### Added

- Added digit-programmer utility
- Added quick start guide for DIGIT manufacturing and assembly
- Added adaptors for DIGIT sensor

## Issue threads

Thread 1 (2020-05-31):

digit vs digit-flex

b4be1, 2020-05-31:
Dear digit-design team,

I want to fabricate the digit sensor. In the `hardware` directory, there are two options: `digit` and `digit-flex`. Are these two different version of the sensor or are these different parts of the same sensor and I need to fabricate them both?

b4be1, 2020-06-01:
Ok, I think `digit` refers to the camera PCB (Fig. 2F in the [paper](https://arxiv.org/pdf/2005.14679.pdf)) and `digit-flex` refers to the lighting PCB (Fig. 2D). So, one needs to manufacture both.

I am trying to submit an order with https://www.pcbway.com/, but there are many options that need to be specified for fabrication which are not stated in the paper. It would be nice if you provide instructions on how to fabricate the sensor.

b4be1, 2020-06-01:
For example, is `digit` a 2-layer board or 4-layer? There are files
```
digit_copper_signal_1.gbr
digit_copper_signal_2.gbr
digit_copper_signal_bot.gbr
digit_copper_signal_top.gbr
```
Does this mean it is a 4-layer board? In which order should these layers go?

AlphaBetaPhi, 2020-06-01:
Hi @b4be1,

We will be releasing a quick-start guide outlining the assembly process. Please see the image below for manufacturing specifications.

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

The DIGIT top level assembly contains two PCB's, the main 4 layer PCB and the flex lighting PCB.

AlphaBetaPhi, 2020-06-01:
Hi @b4be1,

We have uploaded the quick start guide which contains more detailed information for the manufacturing and assembly of the device.

https://github.com/facebookresearch/digit-design/blob/master/DIGIT_Quick_Start_Guide_v1.pdf

robertocalandra, 2020-06-01:
This should answer the question :) Closing the issue. feel free to open a new one if you have more questions.

Closed 2020-06-01.

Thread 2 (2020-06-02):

Microcontroller FT900Q-R is obsolete. Should it be replaced with FT900Q-C-R?

b4be1, 2020-06-02:
It seems the FTDI microcontroller FT900Q-R is not available anymore, see e.g. https://www.mouser.de/ProductDetail/Bridgetek/FT900Q-R?qs=cGEy3R83DS9XW6la3MeywQ==

It should probably be replaced with the newer version FT900Q-C-R. I guess that should work, right?

AlphaBetaPhi, 2020-06-02:
Hei @b4be1,

The DIGIT is based off of the FT900Q series, silicon revision C. At the time of design engineering samples of silicon revision C were available through the FT900Q-R part number. This is equivalent to FT900Q-C-R.

b4be1, 2020-06-02:
Got it, thanks!

nouyang, 2020-08-04:
In case of use; per datasheet for FT900 [e.g here]( https://brtchip.com/wp-content/uploads/Support/Documentation/Datasheets/ICs/MCU/DS_FT900_1_2_3.pdf).
 FT900Q-C-X --> the last letter indicates only product packaging and should be interchangeable.
```
-R: Tape and Reel(Qty per reel is 1000)
-T: Tray packing(Qty per tray for LQFP is 90, qty per tray for QFN is 152
```

Closed 2020-06-02.

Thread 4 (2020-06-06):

About SMT files

chenwh14, 2020-06-06:
Hello,

Thank you for your excellent work!

Could you please export a 'pick and place' file for each PCB design from your original project? It will be helpful for automated SMT component placement, reducing manual work.

Thanks again!

AlphaBetaPhi, 2020-06-06:
Hello @chenwh14,

Thank you for your interest! The files have beed added.

robertocalandra, 2020-06-06:
Closing the issue. Feel free to re-open it if the answer is not of your satisfaction.

Closed 2020-06-06.

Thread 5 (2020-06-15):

Rough cost of electronics?

nouyang, 2020-06-15:
Hello!
Thanks for the release of [all the files](https://github.com/facebookresearch/digit-design/blob/master/releases/DIGIT-fab-release-2020-1.zip) needed to contact a PCB manufacturer for the boards and assembly. I see also there is a [bill of materials](https://github.com/facebookresearch/digit-design/blob/master/hardware/Digit%20BOM%20-%20rev%202020-1.pdf) and a nice [quick start guide](https://github.com/facebookresearch/digit-design/blob/master/DIGIT_Quick_Start_Guide.pdf) It's an amazing amount of work and documentation to be made available to the tactile sensing and robotic manipulation community. I wonder if it's possible to also get a rough sense of the costs at different quantities - e.g. for quantity 5, 10, 50, 100. Apologies as I have only ordered bare PCBs before, this will help me understand whether the cost is reasonable for us to look into. Thanks!

AlphaBetaPhi, 2020-06-15:
Hello @nouyang,

Thank you for your interest and kind words. The pricing entirely depends on the 3rd party manufacturer, assembly type, lead times for the components and PCB's.

If you're looking for an accurate cost figure, I would recommend supplying the release package to various vendors for quoting in those quantities (5, 10, 25, 100, etc). Additionally, if you're looking at hand soldering and assembly, the estimated cost figure for a quantity of 10 is $60-$80 per device. This declines rapidly based on the number of devices being built.

AlphaBetaPhi, 2020-06-16:
Closing this, feel free to re-open or create a new issue.

nouyang, 2020-06-16:
Yes, my apologies for being unclear - I meant that I have not spec'd boards before where the manufacturer also populated the components onto the board, which seems to be recommended in this case. Thank you!

AlphaBetaPhi, 2020-06-16:
Hi @nouyang,

With the manufacturing release package you should be able to get an accurate cost figure for various quantities with automated assembly.  Hope this helps :)

nouyang, 2020-06-17:
Thanks! Yes, I struggled a bit to submit for a quote since it was/is a bit difficult for me to figure out straight-away e.g. number of layers the board has, number of SMT pads, etc.
To clarify, when you say "if you're looking at hand soldering and assembly, "  - I'm actually not sure what that means. Slowly chugging along this process but any tips appreciated :)

nouyang, 2020-07-29:
In case anyone is interested, my quote from pcbway was ~$90 in qty 20 and going down to ~$80 at qty 55. I've made a sheet at tinyurl.com/digit-order & am submitting today. I will look to see if there is option to have circuitboard easily order-able, as they have a "open source" option.

Closed 2020-06-16.

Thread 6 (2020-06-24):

CC-BY-NC license

nouyang, 2020-06-24:
I wanted to confirm my understanding of the license: that the CC-BY-non-commercial applies to the design files themselves and not the manufactured objects (per [explanation](https://www.oshwa.org/sharing-best-practices/) from the open source hardware association).

I ask because I would like to crowdsupply the circuitboards (for economics of scale* and given that I really only want one device). The easiest way would be to make a bulk purchase and then sell it to other researchers. I want to check that I won't run into issues if e.g. I need to add on shipping fees for other researchers.

```
* There is a 17% price break per unit, between Qty 10 and Qty 20, so I would likely aim for a qty 20 group order:

Qty 10 | 20 | 30 | 40 | 55
102.80 | 87.80 | 84.07 | 81.93 | 79.40
```

Thanks!

robertocalandra, 2020-09-10:
I am afraid that we are not lawyers and cannot provide legal advice on your specific use case here.

Closed 2020-09-10.

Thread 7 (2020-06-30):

Layout of LED

lzyplayer, 2020-06-30:
Hi!
Thanks for opening source such great work!

I'm wondering how the rgb light layout on the surface is designed.
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
It seems blue light cover the whole image, while red and green only cross a little compared with gelsight LED layout.(below)
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
Will it be a problem on reconstructing the surface?

Thanks for any reply!

lzyplayer, 2020-07-01:
Another question,
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
the quantities doesn't match current designator. Also, it seems 5 LED is required accroding to [Digit Flex Schematic - rev 2020-1.pdf](https://github.com/facebookresearch/digit-design/blob/master/hardware/Digit%20Flex%20Schematic%20-%20rev%202020-1.pdf)
Thanks for any reply!

AlphaBetaPhi, 2020-07-01:
Hi @lzyplayer,

Thank you for your feedback and interest.

Up to 4 LED's may be included, however, for DIGIT we only populate D1, D2, D3. The compressed release file specifies the populated components in "digit_flex_smt_xy.txt".

I will update the BOM PDF to state that these are optional.

There will be an update to this issue regarding your the initial comment about the lighting configuration.

lzyplayer, 2020-07-01:
Thanks for your quick reply! That solve my latter question.
Really looking forword to the upcomming update!

AlphaBetaPhi, 2020-07-03:
Hi @lzyplayer,

The DIGIT was designed to resemble that of a finger tip. Two LED's (red and green) are offset by 45deg from the center, and the blue LED is directly in the center. I do believe it might impact 3D reconstruction performance but this is something we do not have any numbers to verify this.

lzyplayer, 2020-07-03:
Thanks for your kindly reply! I 'll try some reconstruction work on current DIGIT sensor and share what I found.

Closed 2020-07-03.

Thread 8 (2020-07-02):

Dataset

ucabwl2, 2020-07-02:
Hi

This sensor is awesome. I wonder is there any dataset available online? Thanks.

robertocalandra, 2020-07-02:
Hi ucabwl2,
Thanks for the compliment.
We currently don't have any public dataset collected using DIGIT.
What dataset would you be interested in having in the future?

ucabwl2, 2020-07-02:
Hi
Thanks for your reply. Currently, I'm interested in the dataset like the one collected by GelSight.
https://sites.google.com/view/the-feeling-of-success/

robertocalandra, 2020-07-02:
Ok that's useful feedback. Thanks :)

Closed 2020-07-02.

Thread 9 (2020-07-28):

Firmware update: idVendor correct?

b4be1, 2020-07-28:
The ID that I get when connecting Digit via USB is different from the one in https://github.com/facebookresearch/digit-design/blob/master/firmware/digit-programmer/programmer.yaml, which is `2833:0209 Oculus VR, Inc.`

The ID that I get is `0403:0fde Future Technology Devices International, Ltd`. Is this important? I have not flashed the firmware yet. When I execute `dfu-util -l`, I get

    `Found DFU: [0403:0fde] ver=2300, devnum=6, cfg=1, intf=0, path="1-12", alt=0, name="UNKNOWN", serial="00000000"`

AlphaBetaPhi, 2020-07-30:
Hi @b4be1,

On a fresh build, the FTDI DFU is used with vid/pid `0403:0fde`. Currently, the vid/pid values inside `programmer.yaml` are not enforced. Upon programming the binary file, the device will first boot into DFU mode for 3 seconds with `0403:0fde` and then enumerate with `2833:0209`.

Closed 2020-07-30.

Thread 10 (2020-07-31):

Acrylic_Laser.DXF

vbetancu, 2020-07-31:
Good afternoon,
I have found you work to be very interesting, thanks for sharing.
While trying to open the files I was unable to open the acrylic_laser.dxf. It shows as text but doesn't work with AutoDesk software. Could you please help me?
Thanks

AlphaBetaPhi, 2020-07-31:
Hi @vbetancu,

Thank you for your interest in this work!

Do you have a preferred file format?

vbetancu, 2020-07-31:
I am trying to open it with AutoCad or AutoDesk Fusion, so I believe DXF is good. I am just not sure why it opens as text and can not be read by these software packages.

vbetancu, 2020-08-03:
Maybe if you could help me by re-uploading the file. That might fix the issue. Thanks in advance.

vbetancu, 2020-08-03:
I also had a similar issue with the Gel mold file. AutoDesk was unable to read it.

robertocalandra, 2020-08-03:
Hi @vbetancu,
We tested acrylic_laser.dxf on several machines/softwares (including AutoDesk Fusion 360, and the online viewer https://beta.sharecad.org) and we could not reproduce this issue. For us, everything seems to be working correctly.
I suspect that it might be an issue with your local machine. What OS are you using? can you successfully open other .dxf files?

PS: say Hi to Kimo from me :)

vbetancu, 2020-08-04:
Hi @robertocalandra ,
Thank you for your message. I'll tell Kimo you say hi :)
I think my issue might be with the download of the file as when I click on it on the webpage there is no option to download like the others but it translates into text. Do you recommend any way of downloading it directly from the page? That might solve my issue.

robertocalandra, 2020-08-04:
The best way to download the files is either to manually download the whole github repo from https://github.com/facebookresearch/digit-design/archive/master.zip or (preferably) to git clone the repo. On the main page of the repo (https://github.com/facebookresearch/digit-design) you should see a green button named "Code" that lets you explore these two operations.

vbetancu, 2020-08-04:
Thank you @robertocalandra, that actually solved my problem. I really appreciate your help!

vbetancu, 2020-08-06:
Hi @robertocalandra, from the gel mold I see that you have some holes in the corners. Could I ask you what the purpose of these holes was?

AlphaBetaPhi, 2020-08-06:
Hi @vbetancu,

The holes included in the gel mold are optional for molding low quantities. We have included them as locator holes for mounting plates or an optional self-designed back piece.

vbetancu, 2020-08-07:
Thanks a lot Mike!

Closed 2020-08-03.

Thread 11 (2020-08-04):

Cannot set serial correctly

callmeray, 2020-08-04:
Hi,

Thank you for your great work.

I tried to flash the firmware with a serial number following [https://github.com/facebookresearch/digit-design/blob/master/firmware/digit-programmer/README.md](https://github.com/facebookresearch/digit-design/blob/master/firmware/digit-programmer/README.md) but got "DXXXXX" when connected it using [https://github.com/facebookresearch/digit-interface](https://github.com/facebookresearch/digit-interface)

AlphaBetaPhi, 2020-08-04:
Hi @callmeray,

Thank you for your interest!

Can you provide the command you used to flash the firmware?

callmeray, 2020-08-05:
Thank you for your reply.

The command was `python3 flash.py digit.serial=45`. I think it is more like the interface issue, since I could generate the temporary firmware.

AlphaBetaPhi, 2020-08-05:
Hi @callmeray, can you run `lsusb -v` and see if it reports the correct serial number there?

callmeray, 2020-08-05:
The result is

> Bus 003 Device 021: ID 2833:0209
Device Descriptor:
  bLength                18
  bDescriptorType         1
  bcdUSB               2.00
  bDeviceClass          239 Miscellaneous Device
  bDeviceSubClass         2 ?
  bDeviceProtocol         1 Interface Association
  bMaxPacketSize0        64
  idVendor           0x2833
  idProduct          0x0209
  bcdDevice            1.01
  iManufacturer           1 Facebook
  iProduct                2 DIGIT
  iSerial                 3 DXXXXX
  bNumConfigurations      1
  Configuration Descriptor:
    bLength                 9
    bDescriptorType         2
    wTotalLength          220
    bNumInterfaces          2
    bConfigurationValue     1
    iConfiguration          0
    bmAttributes         0x80
      (Bus Powered)
    MaxPower              500mA
    Interface Association:
      bLength                 8
      bDescriptorType        11
      bFirstInterface         0
      bInterfaceCount         2
      bFunctionClass         14 Video
      bFunctionSubClass       3 Video Interface Collection
      bFunctionProtocol       0
      iFunction               2 DIGIT
    Interface Descriptor:
      bLength                 9
      bDescriptorType         4
      bInterfaceNumber        0
      bAlternateSetting       0
      bNumEndpoints           1
      bInterfaceClass        14 Video
      bInterfaceSubClass      1 Video Control
      bInterfaceProtocol      0
      iInterface              2 DIGIT

AlphaBetaPhi, 2020-08-05:
@callmeray,

Thank you, looks like the serial is reported as `iSerial 3 DXXXXX`.

Can you `git pull` from the repo and then run this command,

`python3 flash.py digit.firmware="../digit-2020-1b.bin" digit.serial=45`

callmeray, 2020-08-05:
I got the same result.

>  idVendor           0x2833
  idProduct          0x0209
  bcdDevice            1.01
  iManufacturer           1 Facebook
  iProduct                2 DIGIT
  iSerial                 3 DXXXXX

Does it require a specified python version? I'm using Python 3.7.7.

AlphaBetaPhi, 2020-08-05:
@callmeray,

May you post the output of `flash.py`?

callmeray, 2020-08-06:
Thanks. It works this time. The reason I failed should be that DIGIT was plugged when I run `flash.py`.

robertocalandra, 2020-08-06:
Glad to hear that this fixed the problem. I am closing the issue; feel free to reopen if you encounter more problems.

Closed 2020-08-06.

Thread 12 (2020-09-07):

Questions regarding materials to build the sensor.

ErickRosete, 2020-09-07:
1.- According to the Quick Start Guide the gel acrylic window is cut from a sheet of 4 mm thick optically clear acrylic, but checking the step files available I found that the thickness of the 3D model is 6.15 mm, which is the appropriate dimension?
2.- According to the Quick Start Guide Smooth-On Solaris the shore hardness is 10A, but the only product available in the official webpage https://www.smooth-on.com/products/solaris/  says the shore hardness is 15A, is it a different product?

AlphaBetaPhi, 2020-09-10:
@ErickRosete, thank you for your interest and questions.

1. This can be cut from a 6 mm sheet of optically clear acrylic (will update this in the guide), in either case, this can be built with whichever size between 4-6.2 mm acrylic panel is available.
2. You may order the product shore 15A product from Smooth-On, we have found through internal testing that the gel design results in shore hardness 10 using the shore 15A product. Additionally, you may use the Smooth-On Slacker product to change shore hardness.

We will add additional notes to the gel instructions to address these issues and provide some insight onto changing gel parameters for end applications.

Closed 2020-09-10.

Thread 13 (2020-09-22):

U2 (OVM7692-RAAA) not available to purchase

robotfan32123, 2020-09-22:
Hi Everyone! First thing first: Great Project!
We'd love to build some test units of the digit but unfortunately found that its impossible to source U2 (OVM7692-RAAA) over here in Germany. We tried every supplier we know but only find it in the US (export restrictions don't allow digikey to ship it here from their US facilities). OmniVision themself only start selling >10k units/year.

Are you aware of this issue and do you maybe have a solution/replacement for this?

Thanks in advance!

AlphaBetaPhi, 2020-09-22:
Hi @robotfan32123, thank you for your interest in the project!

Thank you for bringing this up. Currently, there is no replacement to the OVM7692 sensor.

However, it is recommended to build this through a fabrication house due to the fine pitched/BGA components on the PCB. The fabrication release package may be sent to a number fabrications house for builds which will use their established supply chains, have you tried this?

robotfan32123, 2020-09-22:
Thanks for the quick reply, @AlphaBetaPhi
Yes, we tried 2 different EMS' we usually comission for fabrication (one of them being quite big here in Germany) but both of them struggle to source the sensor.
They even tried to alternatively source from a HK based supplier or directly contacted OmniVision but had no success (unless we order >10k units.)

Is it possible to DM you for this? Maybe we can find a different way of sourcing the components or assembled PCBs.

AlphaBetaPhi, 2020-09-22:
Hi @robotfan32123,

Feel free to reach out offline at lambetam [at] fb.com

Qianboy, 2021-01-07:
Hi all,

We are also super willing to try this sensor out here in Germany, since we are also facing this issue, can you please introduce a bit on how to source the missing components? Thanks a lot!

AlphaBetaPhi, 2021-01-08:
Hi @Qianboy,

May you reach out to me at lambetam[at]fb.com

Thank you,

Mike

robertocalandra, 2021-01-08:
We are aware that unfortunately sourcing the OVM7692 can be complicated in some countries, but we do not plan to support other cameras at the time being.
I am closing the issue, but for anybody encountering this issue now and in the future, please get in touch directly with @AlphaBetaPhi at lambetam[at]fb.com and we will try our best to assist.

Closed 2021-01-08.

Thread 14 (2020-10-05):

High resolution pictures of the assembled boards

nouyang, 2020-10-05:
I am being asked to verify parts orientations for the boards by the PCB manufacturer  - would it be possible to add high res pictures of the front and back of the boards to this repository, so I may send to them directly? (There are a few in the quick start guide but more appreciated). Thanks!

AlphaBetaPhi, 2020-10-19:
Hi @nouyang,

I have updated:

* the fab release package with the assembly view PDF's
* included adhesive outline in the lighting flex pcb gerber files.

Do you have high quality photos you would like to contribute to the repository?

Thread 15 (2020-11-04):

Programming Digit Device

vbetancu, 2020-11-04:
Good evening,

I was trying to flash the firmware for the Digit device but it seems like the instructions (at least for the programmer) are for Linux. Do you have instructions for Windows by chance?

Thanks in advance,
Veronica

AlphaBetaPhi, 2020-11-05:
Hello @vbetancu,

Thank you for your interest.

You may follow the link in this post to download the toolchain for Windows.

https://github.com/facebookresearch/digit-interface/issues/3#issuecomment-657252046

vbetancu, 2020-11-05:
Thank you for your response. I followed the instructions from the other post and downloaded the toolchain and flashed "digit-2020-1b.bin" to the device.
Then I went to the programmer and changed the serial to D00001.
What would be the next step?

vbetancu, 2020-11-05:
I unplugged and plugged back device and now it's recognized. Then I followed installation instructions in this link:https://github.com/facebookresearch/digit-interface/blob/master/README.md
How to proceed for the usage section? Spyder or similar?

AlphaBetaPhi, 2020-11-09:
Hi @vbetancu,

I have attached a picture for future reference on Windows programming.

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

The DIGIT interface currently only supports Linux based operating systems. However, to use DIGIT on Windows you can initialize the DIGIT class without a serial number and then populate the device name using the OpenCV device ID (in this example it is 0):

```
from digit_interface.digit import Digit

d = Digit(name="DIGIT Dev 0")
d.dev_name = 0

d.connect()
d.show_view()
d.disconnect()
```

vbetancu, 2020-11-18:
Thank you very much Mike.
I was able to get the device to stream video but it's not able to take single frames. I am following the procedure in the read me file. Am I missing something?

from digit_interface.digit import Digit
d = Digit("DXXXXX") # Unique serial number
d.connect()
frame = d.get_frame()
print(f"Frame WxH: {frame.shape[0]}{frame.shape[1]}")

AlphaBetaPhi, 2020-11-18:
Hi @vbetancu,

We do not support connecting to the serial number of the device on Windows platforms. Please try the following,

```
from digit_interface.digit import Digit

d = Digit(name="DIGIT Dev 0")
d.dev_name = 0
d.connect()

frame = d.get_frame()
print(f"Frame WxH: {frame.shape[0]}{frame.shape[1]}")
```

vbetancu, 2020-11-18:
Thank you Mike. I actually switched to a Linux operating system when trying to implement the code in the previous message.

AlphaBetaPhi, 2020-11-18:
What does the output show?

vbetancu, 2020-11-18:
runfile('/home/gelsight/.config/spyder-py3/temp.py', wdir='/home/gelsight/.config/spyder-py3')
Frame WxH: 320240

But it didn't take a picture

vbetancu, 2020-11-18:
That's the output I get after running:
from digit_interface.digit import Digit
d = Digit("DXXXXX") # Unique serial number
d.connect()
frame = d.get_frame()
print(f"Frame WxH: {frame.shape[0]}{frame.shape[1]}")

AlphaBetaPhi, 2020-11-18:
`d.get_frame()` returns a frame into the variable `frame` which can then later be used for processing in the application. This does not save the frame. To do this,

```
from digit_interface.digit import Digit
d = Digit("DXXXXX") # Unique serial number
d.connect()
frame = d.save_frame()
```

vbetancu, 2020-11-18:
That worked! Thank you MIke!

AlphaBetaPhi, 2020-11-18:
Great to hear @vbetancu, closing this issue.

Closed 2020-11-18.

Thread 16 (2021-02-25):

Markers in gel: getting "actual" force estimates

vincentmaye, 2021-02-25:
Hey Digit-Team,

fantastic work thanks for making it available!

I was wondering if you could share your experiences with adding markers / reference particles into the gel to estimate forces based on marker displacements, since I saw one elastomer with markers in the paper but no further explanation?

1. How much does this complicate the manufacturing process and
2. how accurate could the estimated forces be?

Thanks!

AlphaBetaPhi, 2021-06-28:
Hi @vincentmaye,

There are a number of methods to add markers on the gels,

- print them on with a UV printer (or any other suitable method) and then cover with the white image transfer layer
- laser etch them onto the surface of the white image transfer layer

Closed 2021-09-07.

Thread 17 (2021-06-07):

Airbrush

luarss, 2021-06-07:
Hi,

First of all, thanks for making this sensor open-source! I am looking to purchase the items and am not sure what sort of airbrush is required for the mold. If anyone could let me know that would be great!

AlphaBetaPhi, 2021-06-07:
Hi @luarss,

Thank you for your interest in the project.

We recommend the following: Iwata-Medea Eclipse HP CS Dual Action Airbrush Gun / Gravity Feed.

luarss, 2021-06-07:
Wow that is expensive. Do you have any recommendations as to the tip size we should use for the spraying?

Closed 2021-06-07.

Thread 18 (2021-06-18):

CMOS OVM7692-RAAA and LEDs ARGB1313HS-TR are not available. Replacement possible?

b4be1, 2021-06-18:
Hi @AlphaBetaPhi,

I contacted several companies to produce the PCBs recently, and all of them unfortunately confirmed that it is not possible to get the camera and the LEDs at the moment. Is it possible to replace those parts with similar ones? If yes, could you recommend the suitable parts?

Best,
Boris

AlphaBetaPhi, 2021-06-18:
Hi @b4be1,

There is a wide shortage of components accross many different vendors.

We have identified some replacements,

Camera - replace with OVM7692-RYAA
LED's - replace with 19-337C/RSBHGHC-A88/4T (this requires a design change to the flex lighting PCB)

New design for flex lighting PCB will be made available shortly.

Thank you,

Mike

b4be1, 2021-06-18:
Thank you very much for the quick reply. This is really good news!

b4be1, 2021-06-28:
Hi Mike,

I got a confirmation that the parts you suggested are all available. As I understood from your reply, the main PCB can be produced using the old design files by just substituting the camera, but for the flexible LED strip I should wait a bit for the new design files, right?

Best,
Boris

tkelestemur, 2021-06-28:
@b4be1 FYI, I was able to get a quote from Imagineering, Inc. with the original LED in the current BOM list and OVM7692-RYAA camera but they can't find the FT900Q-R sensor so I'm trying to find a substitute for them.

b4be1, 2021-06-28:
Thanks for the info @tkelestemur! You can replace FT900Q-R with FT900Q-C-T. I already produced the PCB with this newer microcontroller and everything works fine.

tkelestemur, 2021-06-28:
Yeah, that's what @AlphaBetaPhi told me to do. Where did you order your PCBs from? The manufacturer I'm talking to is saying it's gonna take 3 weeks and I'm wondering if I can find somewhere else that'll do it faster.

b4be1, 2021-06-28:
Yes, for me the waiting time is the same. I ordered from PCBWay.com

AlphaBetaPhi, 2021-06-28:
Hi @tkelestemur, @b4be1, unfortunately with this global shortage a lot of parts are out of stock. There is some available stock but most likely it would need to be purchased and shipped to the PCBA manufacturer (https://octopart.com/search?q=FT900Q-C-T&currency=USD&specs=0).

As for the flex design, there will be an update to this repo today. I'll be pushing the updated design.

AlphaBetaPhi, 2021-06-28:
Hi all,

I have pushed rev. 2021-2 for the Digit Flex PCB to, [digit flex rev 2021-2](https://github.com/facebookresearch/digit-design/tree/master/hardware/fabrication/digit-flex/2021-2)

Additionally, for part swaps see [design notes](https://github.com/facebookresearch/digit-design#design-notes) for updates on part shortages and comments on acceptable part substitutions.

tkelestemur, 2021-06-29:
Thanks @AlphaBetaPhi

b4be1, 2021-06-29:
Many thanks @AlphaBetaPhi!

b4be1, 2021-06-29:
One small question: in [Digit BOM](https://github.com/facebookresearch/digit-design/blob/master/hardware/Digit%20BOM%20-%20rev%202020-1.pdf), the quantity of LED's is specified as 3 but there are 5 diodes D1-D5 in the schematic [Digit Flex Schematic](https://github.com/facebookresearch/digit-design/blob/master/hardware/Digit%20Flex%20Schematic%20-%20rev%202021-2.pdf). Is it a change in design and there are now 5 LEDs? That would mean I need to adjust the casing too, right?

AlphaBetaPhi, 2021-06-29:
Hi @b4be1, that's correct. There are 5 diodes in the schematic to allow for the addition of extra/optional lighting. The mechanical design is already accounting for these 2 extra LED's.

This is not currently supported at the moment but has been provisioned for future firmware releases.

b4be1, 2021-06-29:
Got it, thanks!

Closed 2021-06-29.

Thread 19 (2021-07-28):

Doubts on the design of the acrylic clip

gabrielecaddeo, 2021-07-28:
Hi everyone,

thank you for the great sensor design that you made publicly available.

Me and my team reproduced the Digit and we noticed some incoherencies in the design of the mechanical components. We were wondering if the provided design files are correct and, in this case, we would like to highlight some issues we encountered.

The STL files of the acrylic clip (with or without snap) show a different representation of the component with respect to the one in the QuickStartGuide. As you can see in these pictures, the one in the Guide has some “windows” that prevent the noise due to a direct illumination of the camera by the LEDs light. The actual version in the STL files has not windows instead. Using the current design, generates unwanted artifacts in the output of the camera as you can see in the following picture. Artifacts due to the green and red LEDs are not visible in the output thanks to the presence of some protrusions in the main case.

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

Hence, we were wondering if that is normal or if there are some inconsistencies in the files in the git repository.

Thanks!

AlphaBetaPhi, 2021-08-10:
Hi @gabrielecaddeo,

Thank you for raising these issues. There will be an update shortly with the latest revision.

This reflection should be solved with the updated acrylic clip file.

gabrielecaddeo, 2021-08-11:
Hi @AlphaBetaPhi,

Thanks for the answer. Looking forward to see the latest revision.

Thank you again.

AlphaBetaPhi, 2021-08-12:
Latest revision pushed, closing this issue.

Closed 2021-08-12.

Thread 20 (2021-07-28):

Field of view reduced with respect to the gel size

gabrielecaddeo, 2021-07-28:
Hi everyone,

thank you for the great sensor design that you made publicly available.

Me and my team reproduced the Digit and we noticed some incoherencies in the design of the mechanical components. We were wondering if the provided design files are correct and, in this case, we would like to highlight some issues we encountered.

We tested the DIGIT and we had quite a good output. However, as it is possible to see in this video, the field of view seems reduced with respect to what were expecting. Indeed, even if the screw driver head is touching on the available surface of the gel, we cannot se its fingerprint on the output image.

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

Hence, we were wondering if that is normal or if there are some inconsistencies in the files in the git repository.

Thanks!

AlphaBetaPhi, 2021-08-10:
Hi @gabrielecaddeo,

Thank you for this issue and your teams interest in the project.

We have alternative designs with longer slightly longer housing the allow for full FOV but with some black edges due to non-square gel (the top of the finger tip)

Is this something that you would be interested in 3D printing?

gabrielecaddeo, 2021-08-11:
Hi @AlphaBetaPhi,

Thanks for the answer. Yes, we would be interested in the alternative design. We would be happy if you can share it with us, if that is not a problem.

Thank you again.

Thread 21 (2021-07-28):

Sizes of screws do not match between main and back cases

gabrielecaddeo, 2021-07-28:
Hi everyone,

thank you for the great sensor design that you made publicly available.

Me and my team reproduced the Digit and we noticed some incoherencies in the design of the mechanical components. We were wondering if the provided design files are correct and, in this case, we would like to highlight some issues we encountered.

The back case and the main case are kept together by means of screws. In the STL files of the backhousing and of the main housing (both with or without snap) it is possible to see that the diameter of the screws does not match. The right screw for the back case is an M2 (and also for the main PCB), while the diameter of the main case suggests the use of an M4.
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

Hence, we were wondering if that is normal or if there are some inconsistencies in the files in the git repository.

Thanks!

AlphaBetaPhi, 2021-08-10:
Hi @gabrielecaddeo,

Thank you for raising this issue. An update with the latest revision will be pushed to the github repository. The designs are identical in terms of size but the mounting features are slightly different.

gabrielecaddeo, 2021-08-11:
Hi @AlphaBetaPhi,

Thanks for the answer. Looking forward to see the latest revision.

Thank you again.

AlphaBetaPhi, 2021-08-12:
Hi @gabrielecaddeo,

The latest mechanical revision has been pushed. Note, the new design contains open holes on the back of the center body enclosure. These will need to be covered by a black tape.

Closed 2021-09-07.

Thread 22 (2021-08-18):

type of the Optically Clear Adhesive

lianghongzhuo, 2021-08-18:
Hi, thank you very much for your great work and sharing.
Just to be sure, is the link below exactly what you used to glue the sensor?
https://www.amazon.de/SilPoxy-Silikon-Kleber-3-g-Tube/dp/B00IRC1YI0
https://www.smooth-on.com/products/sil-poxy/
Because I didn't see in the instruction that this type of glue is optically clear.
Thanks in advance!

AlphaBetaPhi, 2021-08-20:
Hi @lianghongzhuo,

This is an acceptable glue to use. The best technique we found is to place a pea sized blob in the center of the acrylic window and then place the silicone gel on top spreading out the glue from the center until it ejects from the sides. This prevents bubbles or streak lines when the glue dries.

Closed 2021-08-20.

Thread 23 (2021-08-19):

Can't install latest firmware [digit-2021-2a]

tkelestemur, 2021-08-19:
We have successfully built our first digit and started testing. After we ran the digit-programmer to install the firmware, we tried the examples in the digit interface. It works without a problem, however, in the output, the example warns that we need to use the latest firmware for independent RGB intensity control (see below). To install the latest firmware, we tried to flash the digit-2021-2a by running the following command: `python flash.py digit.firmware="../digit-2021-2a.bin"` but it failed with the following error:
```
(phd) ➜  digit-programmer git:(master) ✗ python flash.py digit.firmware="../digit-2021-2a.bin"
DIGIT programmer config:
INFO:DigitProgrammer:Attempting to find DIGIT serial mask in ../digit-2021-2a.bin binary.
INFO:DigitProgrammer:Found serial pattern...
INFO:DigitProgrammer:Serial number written to new firmware binary.
INFO:DigitProgrammer:Flashing DIGIT firmware...
Unplug and plug DIGIT into usb then press ENTER...
dfu-util 0.9

Copyright 2005-2009 Weston Schmidt, Harald Welte and OpenMoko Inc.
Copyright 2010-2016 Tormod Volden and Stefan Schmidt
This program is Free Software and has ABSOLUTELY NO WARRANTY
Please report bugs to http://sourceforge.net/p/dfu-util/tickets/

dfu-util: Invalid DFU suffix signature
dfu-util: A valid DFU suffix will be required in a future dfu-util release!!!
dfu-util: No DFU capable USB device available
INFO:DigitProgrammer:Finished flashing firmware to DIGIT!
```
Note that we installed the digit-interface from the source by cloning the master branch. The output of the demo_digit.py can be seen below. Even though, we currently don't need individual RGB intensity control, we wanted to let you know about this issues.
```
(phd) ➜  example git:(master) ✗ python demo_digit.py
DEBUG:digit_interface.digit_handler:Finding udev devices with subsystem=video4linux, id_model=DIGIT
DEBUG:digit_interface.digit_handler:Following udev devices found:
DEBUG:digit_interface.digit_handler:Device('/sys/devices/pci0000:00/0000:00:14.0/usb1/1-1/1-1:1.0/video4linux/video2')
DEBUG:digit_interface.digit_handler:Device('/sys/devices/pci0000:00/0000:00:14.0/usb1/1-1/1-1:1.0/video4linux/video3')
Connected DIGIT's to Host:
[{'dev_name': '/dev/video2',
  'manufacturer': 'Facebook',
  'model': 'DIGIT',
  'revision': '0101',
  'serial': 'D00000'},
 {'dev_name': '/dev/video3',
  'manufacturer': 'Facebook',
  'model': 'DIGIT',
  'revision': '0101',
  'serial': 'D00000'}]
DEBUG:digit_interface.digit:Digit object constructed with serial D00000
DEBUG:digit_interface.digit_handler:Finding udev devices with subsystem=video4linux, id_model=DIGIT
DEBUG:digit_interface.digit_handler:Following udev devices found:
DEBUG:digit_interface.digit_handler:Device('/sys/devices/pci0000:00/0000:00:14.0/usb1/1-1/1-1:1.0/video4linux/video2')
DEBUG:digit_interface.digit_handler:Device('/sys/devices/pci0000:00/0000:00:14.0/usb1/1-1/1-1:1.0/video4linux/video3')
DEBUG:digit_interface.digit_handler:Searching for DIGIT with serial number D00000
INFO:digit_interface.digit:D00000:Connecting to DIGIT
INFO:digit_interface.digit:D00000:Setting stream defaults to QVGA, 60fps, maximum LED intensity.
DEBUG:digit_interface.digit:Default stream to QVGA {'width': 320, 'height': 240}
DEBUG:digit_interface.digit:D00000:Stream resolution set to 240w x 320h
DEBUG:digit_interface.digit:Default stream with 60 fps
DEBUG:digit_interface.digit:D00000:Stream FPS set to 60
DEBUG:digit_interface.digit:Setting maximum LED illumination intensity
WARNING:digit_interface.digit:You are using a previous version of the firmware which does not support independent RGB control, update your DIGIT firmware.
DEBUG:digit_interface.digit:D00000:LED intensity set to 0 (R: 0 G: 0 B: 0
Name: Left Gripper /dev/video2
	- Model: DIGIT
	- Revision: 101
	- CV Device?: True
	- Connected?: True
Stream Info:
	- Resolution: 320 x 240
	- FPS: 60
	- LED Intensity: 0
WARNING:digit_interface.digit:You are using a previous version of the firmware which does not support independent RGB control, update your DIGIT firmware.
DEBUG:digit_interface.digit:D00000:LED intensity set to 0 (R: 0 G: 0 B: 0
WARNING:digit_interface.digit:You are using a previous version of the firmware which does not support independent RGB control, update your DIGIT firmware.
DEBUG:digit_interface.digit:D00000:LED intensity set to 0 (R: 0 G: 0 B: 0
DEBUG:digit_interface.digit:D00000:Stream resolution set to 240w x 320h
DEBUG:digit_interface.digit:D00000:Stream FPS set to 30
Frame WxH: 320240
```

lianghongzhuo, 2021-08-19:
Hi, did you try unplugging the digit before run flash.py, after the code suggests you plug in the digit device, plug in it?

tkelestemur, 2021-08-19:
Yes, that's how we flashed the default firmware. I also wait for a few seconds until I see the digit in the output of `lsusb`.

lianghongzhuo, 2021-08-19:
maybe because the device was flashed to a firmware, then the idVendor and idProduct have changed?
Is your `lsusb` output indicate your device as 0403:0fde or 2833:0209?

tkelestemur, 2021-08-19:
It's `2833:0209`

lianghongzhuo, 2021-08-19:
I don't have the chip in my hand right now to verify my guess, but I think when the id becomes ` 2833:0209` computer recognizes it as a digit sensor, and you can't flash firmware anymore.
Maybe try to flash the board when it still recognizes as ` 0403:0fde`. In 3 seconds after you plugin, it should still recognize as  `0403:0fde`

tkelestemur, 2021-08-19:
You were right, after I replug it, the switches from `0403:0fde` to `2833:0209`. I pressed enter before it changes and I think I was able to flash the new firmware. At least, the example doesn't throw the warning anymore. Here is the output of the flash.py:
```
(phd) ➜  digit-programmer git:(master) ✗ python flash.py digit.firmware="../digit-2021-2a.bin" digit.serial=0
DIGIT programmer config:
INFO:DigitProgrammer:Attempting to find DIGIT serial mask in ../digit-2021-2a.bin binary.
INFO:DigitProgrammer:Found serial pattern...
INFO:DigitProgrammer:Serial number written to new firmware binary.
INFO:DigitProgrammer:Flashing DIGIT firmware...
Unplug and plug DIGIT into usb then press ENTER...
dfu-util 0.9

Copyright 2005-2009 Weston Schmidt, Harald Welte and OpenMoko Inc.
Copyright 2010-2016 Tormod Volden and Stefan Schmidt
This program is Free Software and has ABSOLUTELY NO WARRANTY
Please report bugs to http://sourceforge.net/p/dfu-util/tickets/

dfu-util: Invalid DFU suffix signature
dfu-util: A valid DFU suffix will be required in a future dfu-util release!!!
Opening DFU capable USB device...
ID 0403:0fde
Run-time device DFU version 0110
Claiming USB DFU Interface...
Setting Alternate Setting #0 ...
Determining device status: state = dfuIDLE, status = 0
dfuIDLE, continuing
DFU mode device DFU version 0110
Device returned transfer size 256
Copying data from PC to DFU device
Download	[=========================] 100%        44484 bytes
Download done.
Sent a total of 44484 bytes
state(6) = dfuMANIFEST-SYNC, status(0) = No error condition is present
dfu-util: unable to read DFU status after completion
dfu-util: can't detach
Resetting USB to switch back to runtime mode
dfu-util: error resetting after download
INFO:DigitProgrammer:Finished flashing firmware to DIGIT!

lianghongzhuo, 2021-08-19:
Glad to hear that!

lianghongzhuo, 2021-08-20:
So, is your problem solved or not?

AlphaBetaPhi, 2021-08-20:
Hi all,

Thank you for your interest in the project.

When flashing an initial device, with the latest firmware `2a`, the `-padded.dfu` should be used initially. After this, the DIGIT will accept firmware upgrades without padding. Additionally, the firmware can be re-programmed, or downgraded using the same utility even after the vendor and device ID change.

The device should be power cycled after flashing the firmware.

Closed 2021-08-20.

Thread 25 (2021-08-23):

Solidworks files for the DIGIT housing

tkelestemur, 2021-08-23:
We would like to make some changes to the DIGIT housing parts. We're going to print the gripper mount and the main housing as a single piece. To do so, we were wondering if you can provide Solidworks files instead of the .STL files?

tkelestemur, 2021-08-24:
We found out how to convert STL files to Solidworks files.

Closed 2021-08-24.

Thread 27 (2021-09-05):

Replacing the FT900Q-x with a FT901/2/3Q-x

dornik, 2021-09-05:
Hi everyone, hi @AlphaBetaPhi,

Thanks for sharing your work!

Is it possible to replace the FT900Q-x with another microcontroller of the FT90x series? From the [datasheet](https://docs.rs-online.com/c058/0900766b816a4aa0.pdf) (part numbers on page 3 and pin configurations on pages 8ff) it looks as if the only difference would be the missing Ethernet/CAN bus support on the FT901/2/3Q-x.

Thanks in advance!

AlphaBetaPhi, 2021-09-07:
Hi @dornik,

Thank you for your interest in the project.

It is possible to replace the FT900Q with the 901/2/3 variant. Please note, use the C revision of the silicon - FT90X-Q-C.

dornik, 2021-09-07:
Cool, I'm glad that this works and we will make sure to use the C revision.

Thanks for your help!

Closed 2021-09-07.

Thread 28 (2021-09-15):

Firmware versions

b4be1, 2021-09-15:
What firmware version should one use?

By default, `digit-2020-1b-dfu.bin` is specified

https://github.com/facebookresearch/digit-design/blob/ead7143a6b2e728dde39d9a18e598969253a2efe/firmware/digit-programmer/programmer.yaml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

However, I am getting an error

```
Download        [====================== ]  98%        254464 bytes failed!
state(10) = dfuERROR, status(8) = Cannot program memory due to received address that is out of range
dfu-util: can't detach
Resetting USB to switch back to runtime mode
```

If I use `digit-2020-1b.bin`, then everything is working fine.

With `digit-2021-2a.bin`, I can install it, but then upon connecting to the Digit, the red LED turns off.

With `digit-2021-2a-padded.bin`, I am getting the same download error as above at 96%.

AlphaBetaPhi, 2021-09-17:
Hi @b4be1,

Which version of the digit-interface are you using? Can you pull the latest from the digit-interface repository and try?

b4be1, 2021-09-18:
Hi @AlphaBetaPhi,

Thanks for the explanation. I used the latest version of the digit-interface. I ran the default `-dfu.bin` first (probably successfully, I didn't pay attention) and then tried the other firmware versions. It makes sense then that when I install `-dfu.bin` for the second time, it does not terminate successfully, because it is supposed to be installed only in the beginning.

The only unexpected behavior is then that the red LED turns off when I use `digit-2021-2a.bin`. It does not bother me too much at the moment though, because I can use the other version of the firmware.

AlphaBetaPhi, 2021-09-20:
Hi @b4be1 ,

Can you post the output of

```
from digit_interface.digit_handler import DigitHandler

digits = DigitHandler.list_digits()
```

and then post the following after connecting to that DIGIT using,

```
from digit_interface.digit import Digit

d = Digit("Dxxxxx") # your serial number
d.connect()
print(d.info())
```

b4be1, 2021-09-21:
Hi @AlphaBetaPhi,

I started with a fresh Digit. I first installed `digit-2020-1b-dfu.bin` and then ran the commands you provided. Here is the output

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

Then I installed `digit-2020-1b.bin` and ran the commands. The output was the same. After that, I installed `digit-2021-2a.bin` and got the following output

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

As I said before, the only noticeable difference between `2020-1b` and `2021-2a` is that the red LED stops shining when I run `d.connect()`. The camera stream seems to be OK.

I furthermore did some additional experiments on another fresh Digit. I first installed `2021-2a-padded.bin`. This worked fine. So, basically, I am able to either install `2020-1b-dfu.bin` or `2021-2a-padded.bin` as the initial firmware. After that, I am able to install `2020-1b` or `2021-2a`, but I can't install `-dfu` or `-padded` versions anymore because they seem to run out of memory at around 96%–98%.

One thing is still unclear to me: is there a difference between `2020-1b` and `2020-1b-dfu`? It seems all basic functionality is already included in `2020-1b-dfu`.

Some parts had to be replaced in the production of these Digits. I think even the LEDs are different. I attached the materials used in the Digits I am testing on:
[LEDs.pdf](https://github.com/facebookresearch/digit-design/files/7201612/LEDs.pdf)
[PCB.pdf](https://github.com/facebookresearch/digit-design/files/7201614/PCB.pdf)

AlphaBetaPhi, 2021-09-22:
Hi @b4be1,

It looks like the correct firmware is installed, but the digit-interface library version has not been updated as the `LED intensity` is `255`. On new `digit-interface` library this will set the LED intensity to a 12-bit value.

Can you try upgrading the pip package,

`pip install digit-interface --upgrade` and try with the new firmware.

b4be1, 2021-09-23:
Hi @AlphaBetaPhi,

I was on version `0.1.4`. After updating to `0.2.1` everything works fine when using `digit-2021-2a.bin`. LED intensity is 4095 in the test output. Thanks!

Closed 2021-09-23.

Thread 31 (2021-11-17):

device not recognized after flashing: "Device not responding to setup address."

roberttamas98, 2021-11-17:
Flashing the firmware on the Digit doesn't seem to work for me, I tried on different PCs and with different Digits, but got the same result as follows:

Before flashing the Digit and using the following command:
    dmesg | grep usb

I get my latest plugged in usb-device and the microcontroller (FT900) is recognised:
    [3712107.985896] usb 1-7: USB disconnect, device number 120
    [3712113.118788] usb 1-7: new high-speed USB device number 121 using xhct_hcd
    [3712113.268139] usb 1-7: New USB device found, idVendor=0403, idProduct=ofde
    [3712113.268144] usb 1-7: New USB device strings: Mr=1, Product=2, SerialNumber=3
    [3712113.268148] usb 1-7: Product: FT900
    [3712113.268150] usb 1-7: Manufacturer: FTDI
    [3712113.2681537 usb 1-7:
    SerialNumber:00000000

after flashing (following all the the instructions):
    python3 flash.py digit.serial=45

and getting following output:
    INFO:DigitProgrammer:DIGIT programmer config: {'digit': {'serial': 45, 'firmware': '../digit-2020-1b-dfu.bin'}, 'usb': {'idVendor': 10291, 'idProduct': 521}}
    INFO:DigitProgrammer:Attempting to find DIGIT serial mask in ../digit-2020-1b-dfu.bin binary.
    INFO:DigitProgrammer:Found serial pattern...
    INFO:DigitProgrammer:Serial number written to new firmware binary.
    INFO:DigitProgrammer:Flashing DIGIT firmware...
    Unplug and plug DIGIT into usb then press ENTER...
    dfu-util 0.9

    Copyright 2005-2009 Weston Schmidt, Harald Welte and OpenMoko Inc.
    Copyright 2010-2016 Tormod Volden and Stefan Schmidt
    This program is Free Software and has ABSOLUTELY NO WARRANTY
    Please report bugs to http://sourceforge.net/p/dfu-util/tickets/

    dfu-util: DFU suffix CRC does not match
    dfu-util: A valid DFU suffix will be required in a future dfu-util release!!!
    dfu-util: No DFU capable USB device available
    INFO:DigitProgrammer:Finished flashing firmware to DIGIT!

something obviously went wrong, but no idea what and if I try to list all the usb devices again:
    dmesg | grep usb

it doesn't recognize the microcontroller  (FT900) either anymore:
    [ 1766.233552] usb usb1-port6: attempt power cycle
    [ 1766.645491] usb 1-6: new full-speed USB device number 67 using xhci_hcd
    [ 1766.645743] usb 1-6: Device not responding to setup address.
    [ 1766.853783] usb 1-6: Device not responding to setup address.
    [ 1767.061495] usb 1-6: device not accepting address 67, error -71

This was happening with two different digits. After manufacturing another and confirming by "dmesg | grep usb" that the microcontroller is being recognized and before flashing again I also tried:
    sudo dfu-util -l

and got the following output:
    dfu-util 0.8
    Copyright 2005-2009 Weston Schmidt, Harald Welte and OpenMoko Inc.
    Copyright 2010-2014 Tormod Volden and Stefan Schmidt
    This program is Free Software and has ABSOLUTELY NO WARRANTY
    Please report bugs to dfu-util@lists.gnumonks.org
    Found DFU: [0403:0fde] ver=2300, devnum=93, cfg=1, intf=0, alt=0, name="UNKNOWN", serial="00000000"

Does someone else had this issue and got a solution?

AlphaBetaPhi, 2021-11-17:
Hi @roberttamas98,

Thank you for your interest in the project. A few questions:

* Did you manufacture these DIGIT's yourself?
* What MFG part number was used for the FT900, can you list the full part number?

roberttamas98, 2021-11-18:
Thanks for the quick answer
Yes I'm manufacturing them myself.
I have the FT90[1/2/3]-Q-C, but I only used the FT902Q until now.

AlphaBetaPhi, 2021-11-18:
Are you using the FT902Q or FT902Q-C on the devices you assembled?

roberttamas98, 2021-11-18:
I'm using the FT902-Q-C

AlphaBetaPhi, 2021-11-20:
Hi @roberttamas98,

What is the output of `lsusb -vvv' does the DIGIT DFU mode show up?

Can you try this command,

```
$ python flash.py digit.firmware="../digit-2021-2a-padded.bin" digit.serial=123
```

roberttamas98, 2021-11-26:
As I was already suspecting and you suggested, I was using the wrong firmware, but it works now with your command. Is there a possibility to save those digits which where flashed using the wrong firmware?

roberttamas98, 2021-12-06:
Is there someone else experiencing similar issues with flashing the firmware or does someone know if digits where the flashing somehow failed can be saved?

AlphaBetaPhi, 2021-12-07:
@roberttamas98 If you've already flashed the DIGIT and it enumerates as "FT900 DFU Mode" then try flashing with

```
python3 flash.py digit.firmware="../digit-2021-2a.bin" digit.serial=2
```

We will be releasing an updated programmer which signs binaries to resolve this.

roberttamas98, 2021-12-07:
unfortunately it still doesn't seem to work:

python3 flash.py digit.firmware="../digit-2021-2a.bin" digit.serial=2
INFO:DigitProgrammer:DIGIT programmer config: {'digit': {'serial': 2, 'firmware': '../digit-2021-2a.bin'}, 'usb': {'idVendor': 10291, 'idProduct': 521}}
INFO:DigitProgrammer:Attempting to find DIGIT serial mask in ../digit-2021-2a.bin binary.
INFO:DigitProgrammer:Found serial pattern...
INFO:DigitProgrammer:Serial number written to new firmware binary.
INFO:DigitProgrammer:Flashing DIGIT firmware...
Unplug and plug DIGIT into usb then press ENTER...
dfu-util 0.9

Copyright 2005-2009 Weston Schmidt, Harald Welte and OpenMoko Inc.
Copyright 2010-2016 Tormod Volden and Stefan Schmidt
This program is Free Software and has ABSOLUTELY NO WARRANTY
Please report bugs to http://sourceforge.net/p/dfu-util/tickets/

dfu-util: Invalid DFU suffix signature
dfu-util: A valid DFU suffix will be required in a future dfu-util release!!!
Opening DFU capable USB device...
ID 0403:0fde
Run-time device DFU version 0110
Claiming USB DFU Interface...
Setting Alternate Setting #0 ...
Determining device status: state = dfuIDLE, status = 0
dfuIDLE, continuing
DFU mode device DFU version 0110
Device returned transfer size 256
Copying data from PC to DFU device
Download	[=========================] 100%        44484 bytes
Download done.
Sent a total of 44484 bytes
state(6) = dfuMANIFEST-SYNC, status(0) = No error condition is present
dfu-util: unable to read DFU status after completion
dfu-util: can't detach
Resetting USB to switch back to runtime mode
dfu-util: error resetting after download
INFO:DigitProgrammer:Finished flashing firmware to DIGIT!

I guess I'll wait for the updated programmer and try to work with the one that somehow worked, but thanks for the help for now

AlphaBetaPhi, 2021-12-07:
@roberttamas98, could you contact me via lambetam [at] fb [dot] com

Let's see if we can root cause this and post the solution on this issue.

csufangyu, 2021-12-15:
hi, can you solve it?I get the same problem.

roberttamas98, 2021-12-22:
In the live-call with mike, we concluded that those problems are most certainly/definitely hardware related issues.

the following outputs to the dmesg command point to different hardware problems:

[  501.072897] usb 3-6: New USB device strings: Mfr=1, Product=3, SerialNumber=2
[  501.072898] usb 3-6: Product: FT900 DFU Mode
[  501.072899] usb 3-6: Manufacturer: FTDI
[  501.072900] usb 3-6: SerialNumber: FT424242
[  503.671422] usb 3-6: USB disconnect, device number 6
[  635.055100] usb 3-6: new full-speed USB device number 7 using xhci_hcd
[  635.207915] usb 3-6: New USB device found, idVendor=0403, idProduct=0fde, bcdDevice=23.00

most likely a problem with the camera, either a short, no contact to a pin or maybe a broken camera

[  641.686334] usbcore: registered new interface driver uvcvideo
[  641.686335] USB Video Class driver (1.1.1)
[  924.223229] usb 3-6: USB disconnect, device number 8
[  935.020330] usb 3-6: new full-speed USB device number 9 using xhci_hcd
[  935.148318] usb 3-6: device descriptor read/64, error -71
[  935.384328] usb 3-6: device descriptor read/64, error -71
[  935.620302] usb 3-6: new full-speed USB device number 10 using xhci_hcd
[  935.752329] usb 3-6: device descriptor read/64, error -71
[  935.988338] usb 3-6: device descriptor read/64, error -71
[  936.096337] usb usb3-port6: attempt power cycle
[  936.524311] usb 3-6: new full-speed USB device number 11 using xhci_hcd
[  936.524521] usb 3-6: Device not responding to setup address.
[  936.732539] usb 3-6: Device not responding to setup address.
[  936.944282] usb 3-6: device not accepting address 11, error -71
[  937.072313] usb 3-6: new full-speed USB device number 12 using xhci_hcd
[  937.072530] usb 3-6: Device not responding to setup address.
[  937.280522] usb 3-6: Device not responding to setup address.
[  937.488310] usb 3-6: device not accepting address 12, error -71
[  937.488363] usb usb3-port6: unable to enumerate USB device

when not recognized at all it might be due to some problem with the contatcs of the microprocessor which can't be seen from the side
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
pekkykang, 2022-07-10:
I have the same problem, and tested four  PCB with the dmesg command. All got:
[ 4417.712816] usb 1-13: New USB device strings: Mfr=1, Product=3, SerialNumber=2
[ 4417.712822] usb 1-13: Product: FT900 DFU Mode
[ 4417.712826] usb 1-13: Manufacturer: FTDI
[ 4417.712830] usb 1-13: SerialNumber: FT424242
[ 4420.153908] usb 1-13: USB disconnect, device number 112
[ 4422.015339] usb 1-9: new full-speed USB device number 113 using xhci_hcd
[ 4422.164651] usb 1-9: New USB device found, idVendor=0403, idProduct=0fde, bcdDevice=23.00

Does these means I got four broken PCB?

pekkykang, 2022-07-10:
Will these be possible that all four cameras are bad?

AlphaBetaPhi, 2022-07-10:
@pekkykang Did you power cycle the DIGIT?

pekkykang, 2022-07-11:
I think the only thing I can do is change the camera supplier and PCB manufacturer.

AlphaBetaPhi, 2022-07-11:
Hi @pekkykang,

This means that the device has been programmed successfully if the LED's are turning on. If the device does not enumerate as a DIGIT after the LED's are on it means it cannot find or configure the camera. Did you assemble these yourself?

pekkykang, 2022-07-11:
> Hi @pekkykang,
>
> This means that the device has been programmed successfully if the LED's are turning on. If the device does not enumerate as a DIGIT after the LED's are on it means it cannot find or configure the camera. Did you assemble these yourself?

Hi, Phi:

Yes, I assemble these myself. I think I will change the camera supplier and PCB manufacturer.

AlphaBetaPhi, 2022-07-11:
Which camera model number did you use? Do you have any pictures of how you assembled the devices?

If they're hand soldered, I would suggest reflowing the camera once more.

pekkykang, 2022-07-11:
I use OVM7692-RAAA and ask a PCB manufacturer to use SMT to do it
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
.

AlphaBetaPhi, 2022-07-11:
Can you take a close up picture of one of the PCBs?

pekkykang, 2022-07-11:
> Can you take a close up picture of one of the PCBs?
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

AlphaBetaPhi, 2022-07-11:
It looks like the camera has been soldered on incorrectly. The orientation is wrong. This would explain why the camera the device is not booting up.

pekkykang, 2022-07-11:
> It looks like the camera has been soldered on incorrectly. The orientation is wrong. This would explain why the camera the device is not booting up.

Thank you. This helps me very much. I will complain to the manufacturer and ask them to give me the money back😂

AlphaBetaPhi, 2022-07-11:
You could remove the camera with hot air and then correct the orientation, it needs to be rotated 180deg.

pekkykang, 2022-07-11:
> You could remove the camera with hot air and then correct the orientation, it needs to be rotated 180deg.

OK

Closed 2022-07-11.

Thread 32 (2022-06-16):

attaching digit to robotiq 2f-85 gripper

stoic-roboticist, 2022-06-16:
Hi,

I would like to attach the digit sensor to a Robotiq 2F-85 gripper. I printed the supplied adapters, however, I couldn't find anywhere in the documentation of what bolts to use to attach the sensor to the printed adapter? also the holes on the bottom of the digit don't seem threaded, so how can you securely attach the sensor to the adapter?

Thanks in advance for your help.

AlphaBetaPhi, 2022-06-16:
Hi @stoic-roboticist,

The Robotiq 2F-85 uses an M5 screw with the default grippers. The same screw can be used with the DIGIT adapter, which is attached to the DIGIT with an M2 screw (https://www.mcmaster.com/91292A005/ or longer lengths). The screws self tap into the plastic.

Closed 2024-02-05.

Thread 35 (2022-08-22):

DIGIT mounting hole standard

shiba-8ro, 2022-08-22:
I am designing an adapter to mount DIGIT to ROBOTIS OpenMANIPULATOR-X. A question arose during the work.
The DIGIT hole looks like a hole for a 2mm tapping screw. is this correct?
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

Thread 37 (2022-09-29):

Is my self-made digit's Gel is not correct? I feel the image is very strange

pekkykang, 2022-09-29:
Hi, all:

I made some digit sensors by myself and I feel the image from the sensor is very strange.
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
Compared with the image from Tacto emulator and image from the offical websit, my image is lack of three-dimensional.
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
And I also feel the red and green light are too strong. Is my elastomer coating is too thin?
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

Any advice from the community will be extremely helpful to me. Thank you so much.

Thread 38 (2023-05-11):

Difference between acrylic window in commercialized DIGITs and the Quickstart Guide.

gabrielecaddeo, 2023-05-11:
Hi all,
thanks for your amazing work.

I am reproducing the DIGIT sensor and I have some [commercialized](https://www.gelsight.com/product/digit-tactile-sensor/) digit samples too. I was comparing the performances and I decided to open the commercialized DIGIT and I saw a difference in the thickness of the acrylic window. In the specs, it is written the acrylic is laser cut from a 4mm thick acrylic, but the one commercialized is 5.5 mm thick. I think the 5.5 mm thickness is the right one, otherwise the acrylic would not fit perfectly in the black top case. Is it an error of the specs?
Thank you

AlphaBetaPhi, 2023-05-11:
Hi @gabrielecaddeo, the commercialized version uses injection molded parts and the dimensions have been increased to meet a common width of the acrylic sheet. Both 4mm and 5.5mm can be used depending on the mechanical enclosure, the 3D printable parts in this repository would dictate which acrylic height should be used.

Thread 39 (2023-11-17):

Unstable image

orionsor, 2023-11-17:
Hi,
I am trying to read data from DIGIT as a usb camera and there is a strange segmentation in the image I got as shown below. The image seems to keep scrolling. I have changed many cables and the problem still exists. Does it mean there is something wrong with the sensor or connection? Thanks!

ejharber, 2023-11-27:
That issue is also posted here! Also waiting for an update.

https://github.com/facebookresearch/digit-interface/issues/10

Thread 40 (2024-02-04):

Artefacts in Gel Adhesion Layers within Spec?

elishafer, 2024-02-04:
I recently bought a few Digit sensors and replacement gels from Gelsight.
I was surprised that some of the gels had dust specs, bubbles and pieces of white silicon in the adhesion layer between the acrylic and clear silicone.
Gelsight said the sample photos I sent them are within the QC spec. How would artefacts like these in the following pictures affect inference? What is the QC spec for artefacts in the adhesion/silicon layers?
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

robertocalandra, 2024-02-05:
Hi @elishafer,

Yes, that is indeed a very clear manufacturing issue with the gel.

Unfortunately, you are not the only person to be having issues with the QC of GelSight Inc recently (https://github.com/facebookresearch/digit-interface/issues/15), but there is nothing I can do about it.

Good news is that if you use machine learning to learn models, I don't expect imperfections in the silicone to strongly impact the performance of your model.

elishafer, 2024-02-05:
HI @robertocalandra,
Thank you for your prompt answer. I totally understand that Gelsight is a separate entity and it's nothing to do on your part

> Good news is that if you use machine learning to learn models, I don't expect imperfections in the silicone to strongly impact the performance of your model.
That's a relief

Do you happen to have the QC manufacturing spec for the gel so that I can negotiate with GelSight for a replacement?
I have a feeling that the following gel replacements shouldn't be in spec:

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

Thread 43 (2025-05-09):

Request for Standard .drl Drill Files for PCB Fabrication

zhengbi-yong, 2025-05-09:
I am working on fabricating the PCB for the DIGIT tactile sensor using the design files from the digit-design repository (link). However, I am encountering an issue with the drill files required by my PCB manufacturer.

The repository includes digit-roundholes.txt and digit-slotholes.txt, which appear to be drill files for round and slot holes, respectively. However, these files have a .txt extension and start with %FSTAX25Y25*% instead of the standard %M48 header expected for Excellon drill files. My PCB manufacturer requires drill files in the standard Excellon format with a .drl extension.

Could you please confirm if digit-roundholes.txt and digit-slotholes.txt are the intended drill files, and whether they can be used directly for PCB fabrication? If not, could you provide standard .drl drill files or guide me on how to convert these files to the required format?

Any guidance on this issue, including specific instructions for PCB fabrication or recommendations for manufacturers familiar with these files, would be greatly appreciated.

Thank you for your time and support!

Best regards.

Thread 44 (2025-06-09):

Inconsistant diffusivity of LED lights on commercial DIGIT sensors

bhsong1011, 2025-06-09:
I have bough a few DIGIT sensors from Gelsight, and noticed the side surface roughness of the acrylic plate are different. Some sensors have rough surface, and the others have a very smooth surfaces (assuming change of laser cutter parameters).

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
Watch the LED window under the gel, which is the side of the acrylic plate. Sharpness of lightings is changed due to the difference of the roughness.

[DIGIT Acrylic Plate.pdf](https://github.com/user-attachments/files/20651350/DIGIT.Acrylic.Plate.pdf)

Due to this lighting difference, data distribution of images seems to change and the sensors are not working with end-to-end models such as [NeuralFeels](https://github.com/facebookresearch/neuralfeels) ([this issue](https://github.com/facebookresearch/neuralfeels/issues/2) may seems like suffering the same problem). I have used the tactile transformer (raw image to depth image end-to-end model) of NeuralFeels and it failed the depth reconstruction when using smooth side surface sensors (therefore I assume the change was from rough to smooth).

I noticed that I am not the only one suffering from QC of Gelsight (#15, #40) and this would be a hard thing to solve. I have contacted Gelsight, but I hope Meta FAIR to step in as well and find a quick-fix solution.

Specifically, would it be possible for FAIR to check the DIGIT sensor's acrylic plate side surface roughness used in prior projects from FAIR? If the surface roughness actually causes the data distribution shift problem, maybe making the smooth surface sensors to have the same diffusivity would be a solution (I can only think about applying translucent tape (such as Scotch Magic tape) on the LED window to match a certain diffusivity).

I am concerned that the already-collected tactile datasets may be neutralized due to this problem when we are provided with sensors that collect out-of-distribution data. Although this problem may be detoured by using depth image as a new common data representation using non-official librarys ([digit-depth](https://github.com/vocdex/digit-depth) or [gs_sdk](https://github.com/joehjhuang/gs_sdk)), but as existing datasets are in rgb format and may need the exact sensor to convert the dataset from raw image to depth image makes this situation difficult.

I hope we can find any type of solution for this issue.

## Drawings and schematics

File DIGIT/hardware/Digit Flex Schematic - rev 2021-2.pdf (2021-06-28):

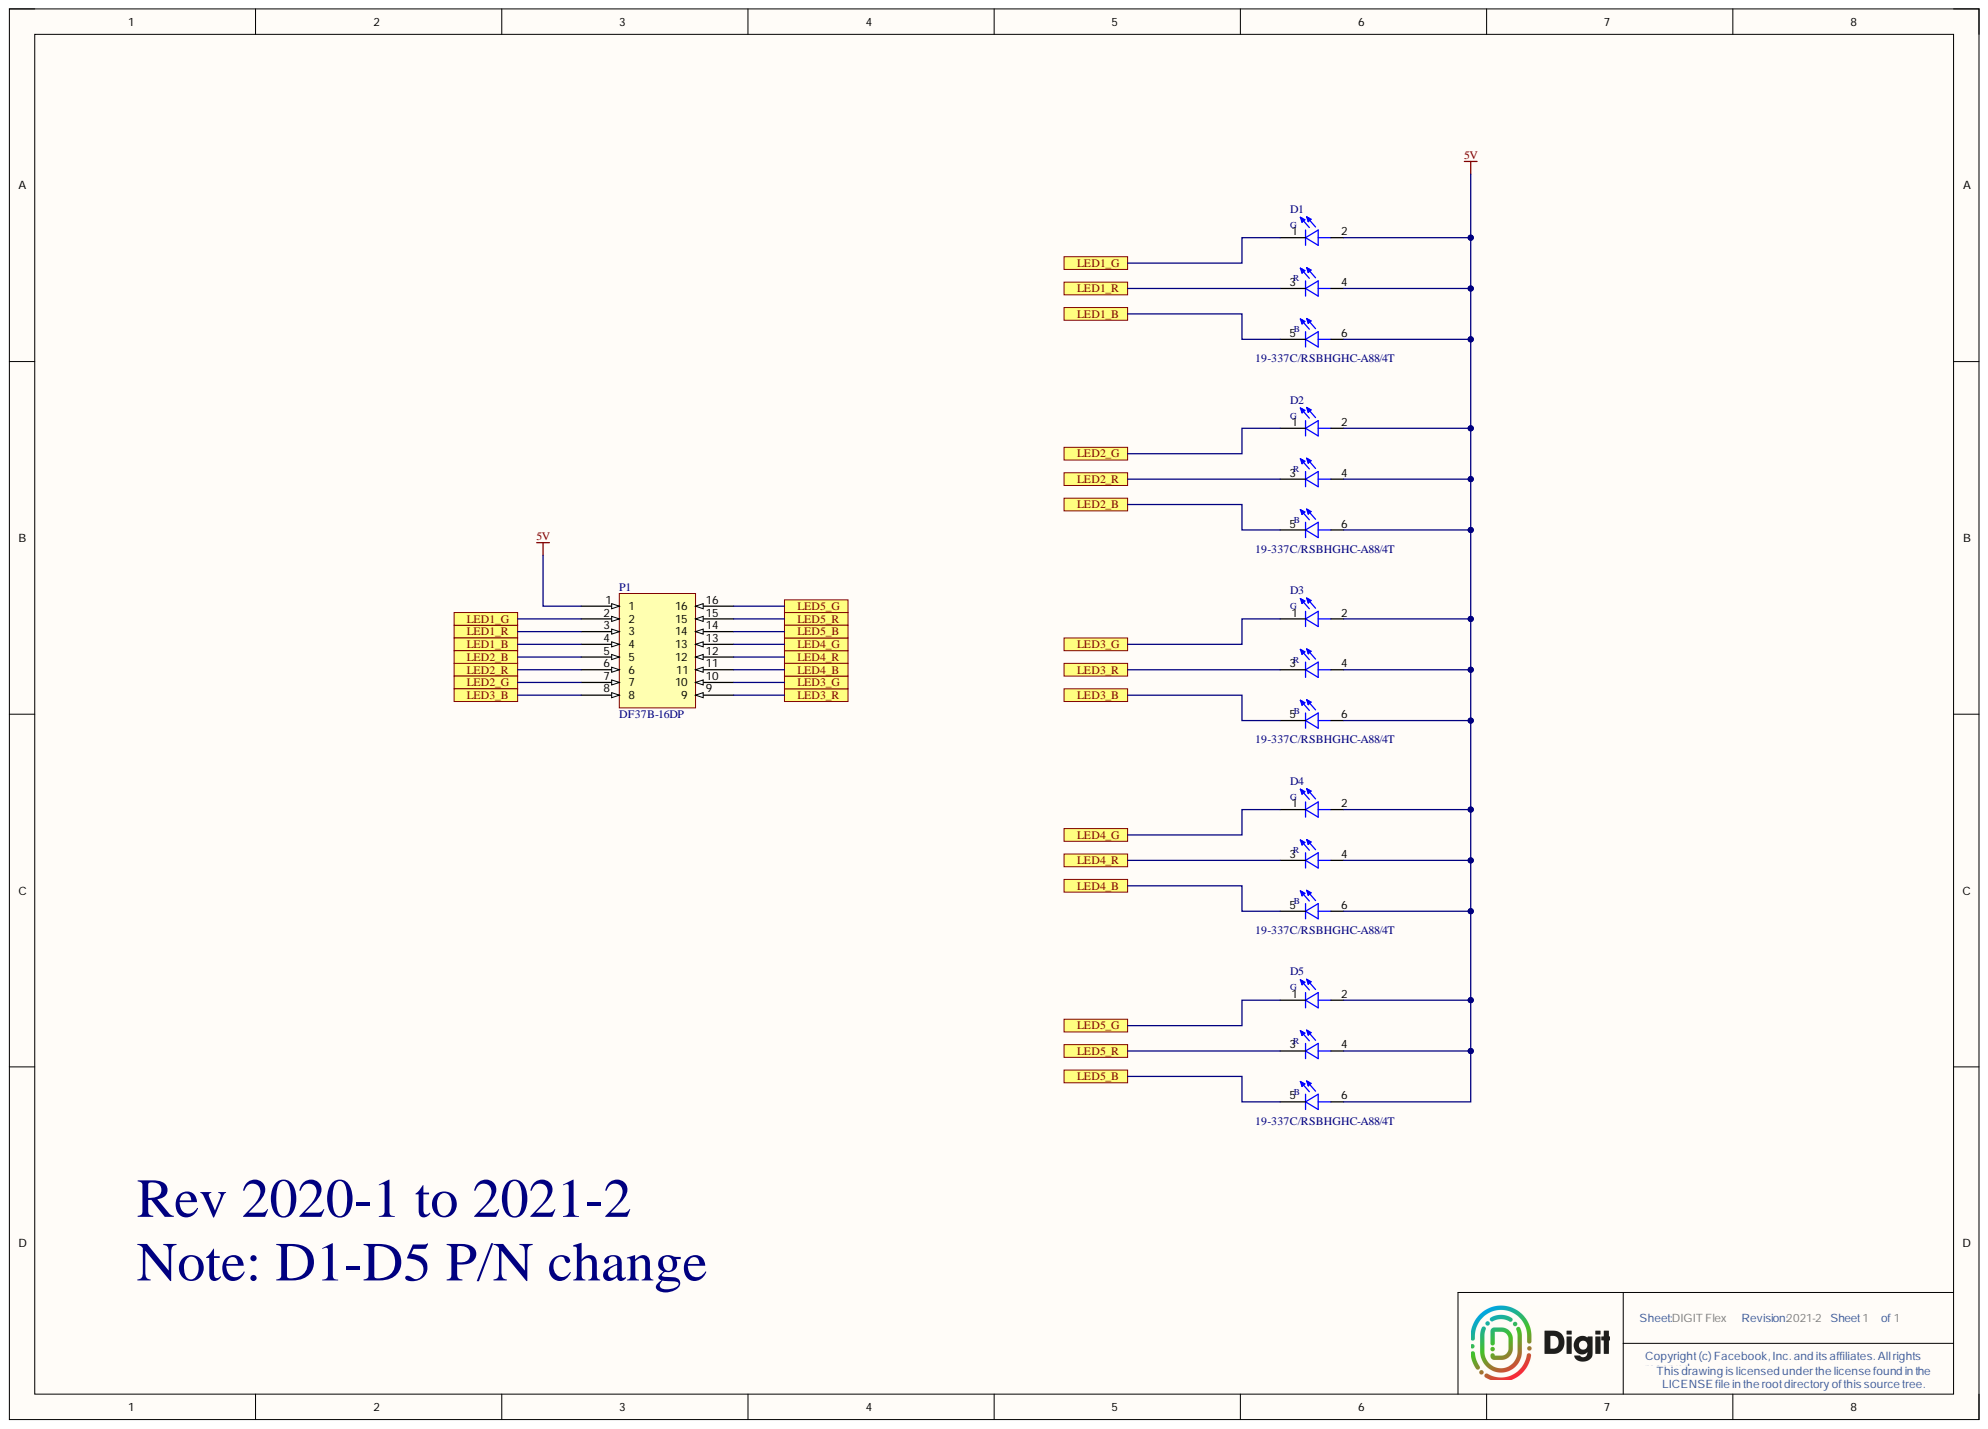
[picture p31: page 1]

LED2_B | 6 6 | LED4_R

Copyright(c)Facebook, Inc. and its affiliates.Allrights
res
LICENSE file in the root directory of this source tree.

Tehrved. is drawing is licensed underthe license found in the

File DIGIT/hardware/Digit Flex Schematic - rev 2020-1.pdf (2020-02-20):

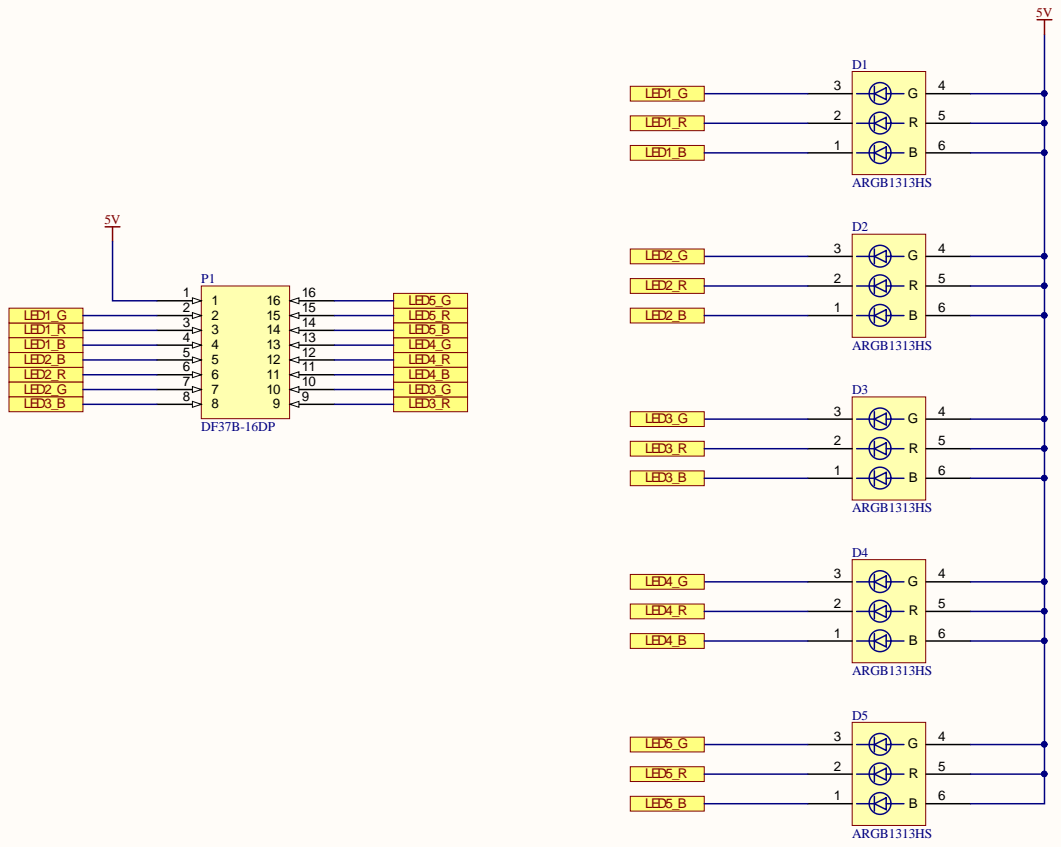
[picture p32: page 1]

LED1_B | 4 4 5 5 | LED4_G | ARGB1313HS D3
LED2_B | 6 6 | LED4_R
LED2_R | 7 7 | LED4_B
LED2_G | | LED3_G
LED3_B | | LED3_R

Copyright (c) Facebook, Inc. and itsaffiliates.All rightsreserved.
This drawing is licensed under the license found in the LICENSE

file in the root directory of this source tree.

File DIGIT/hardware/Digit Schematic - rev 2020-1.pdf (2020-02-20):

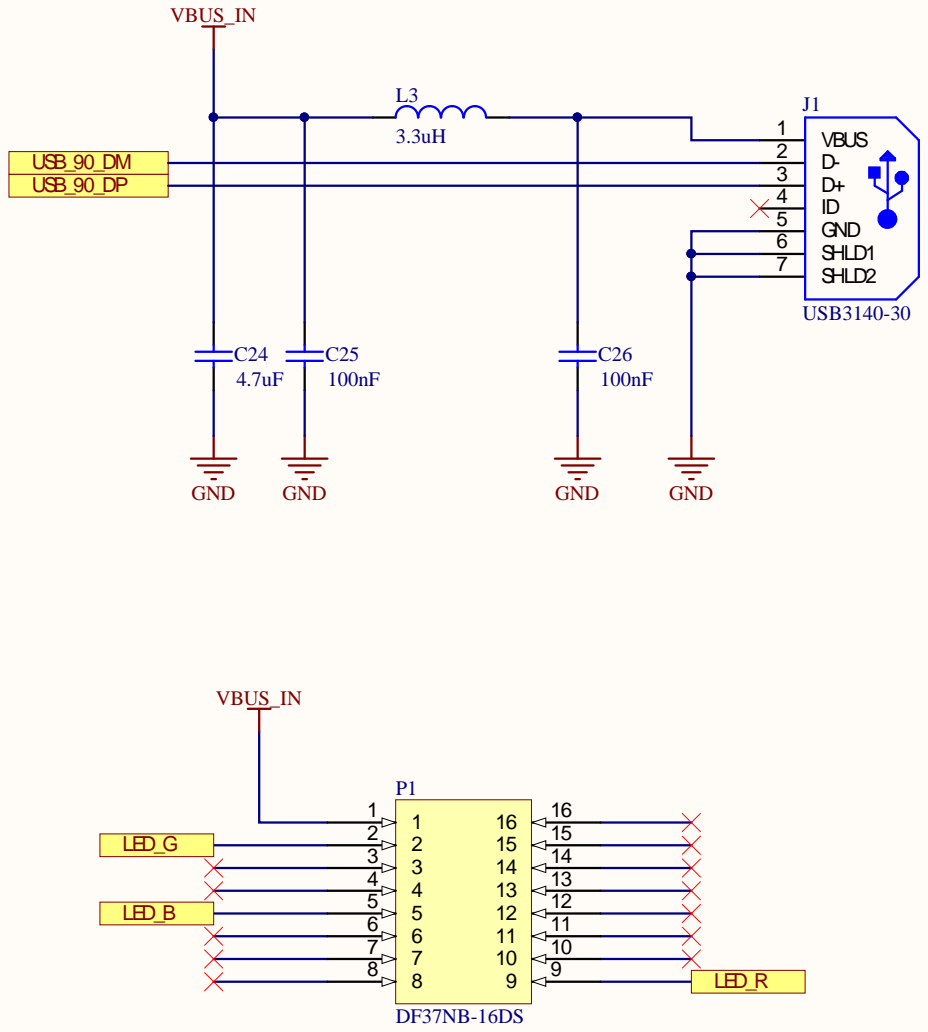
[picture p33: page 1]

USB_90_DP | D+ 3

SHLD1 6
SHLD2 7

LED_G | 3 3

LED_B | 5 5

Copyright (c) Facebook, Inc. and itsaffiliates.All rightsreserved.
This drawing is licensed under the license found in the LICENSE

file in the root directory of this source tree.

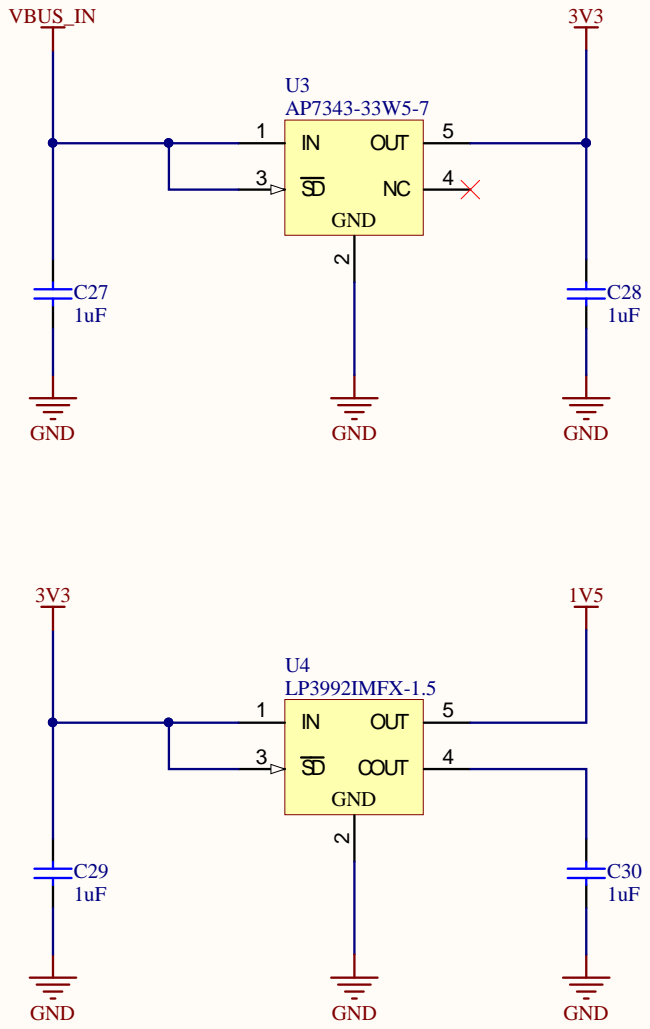
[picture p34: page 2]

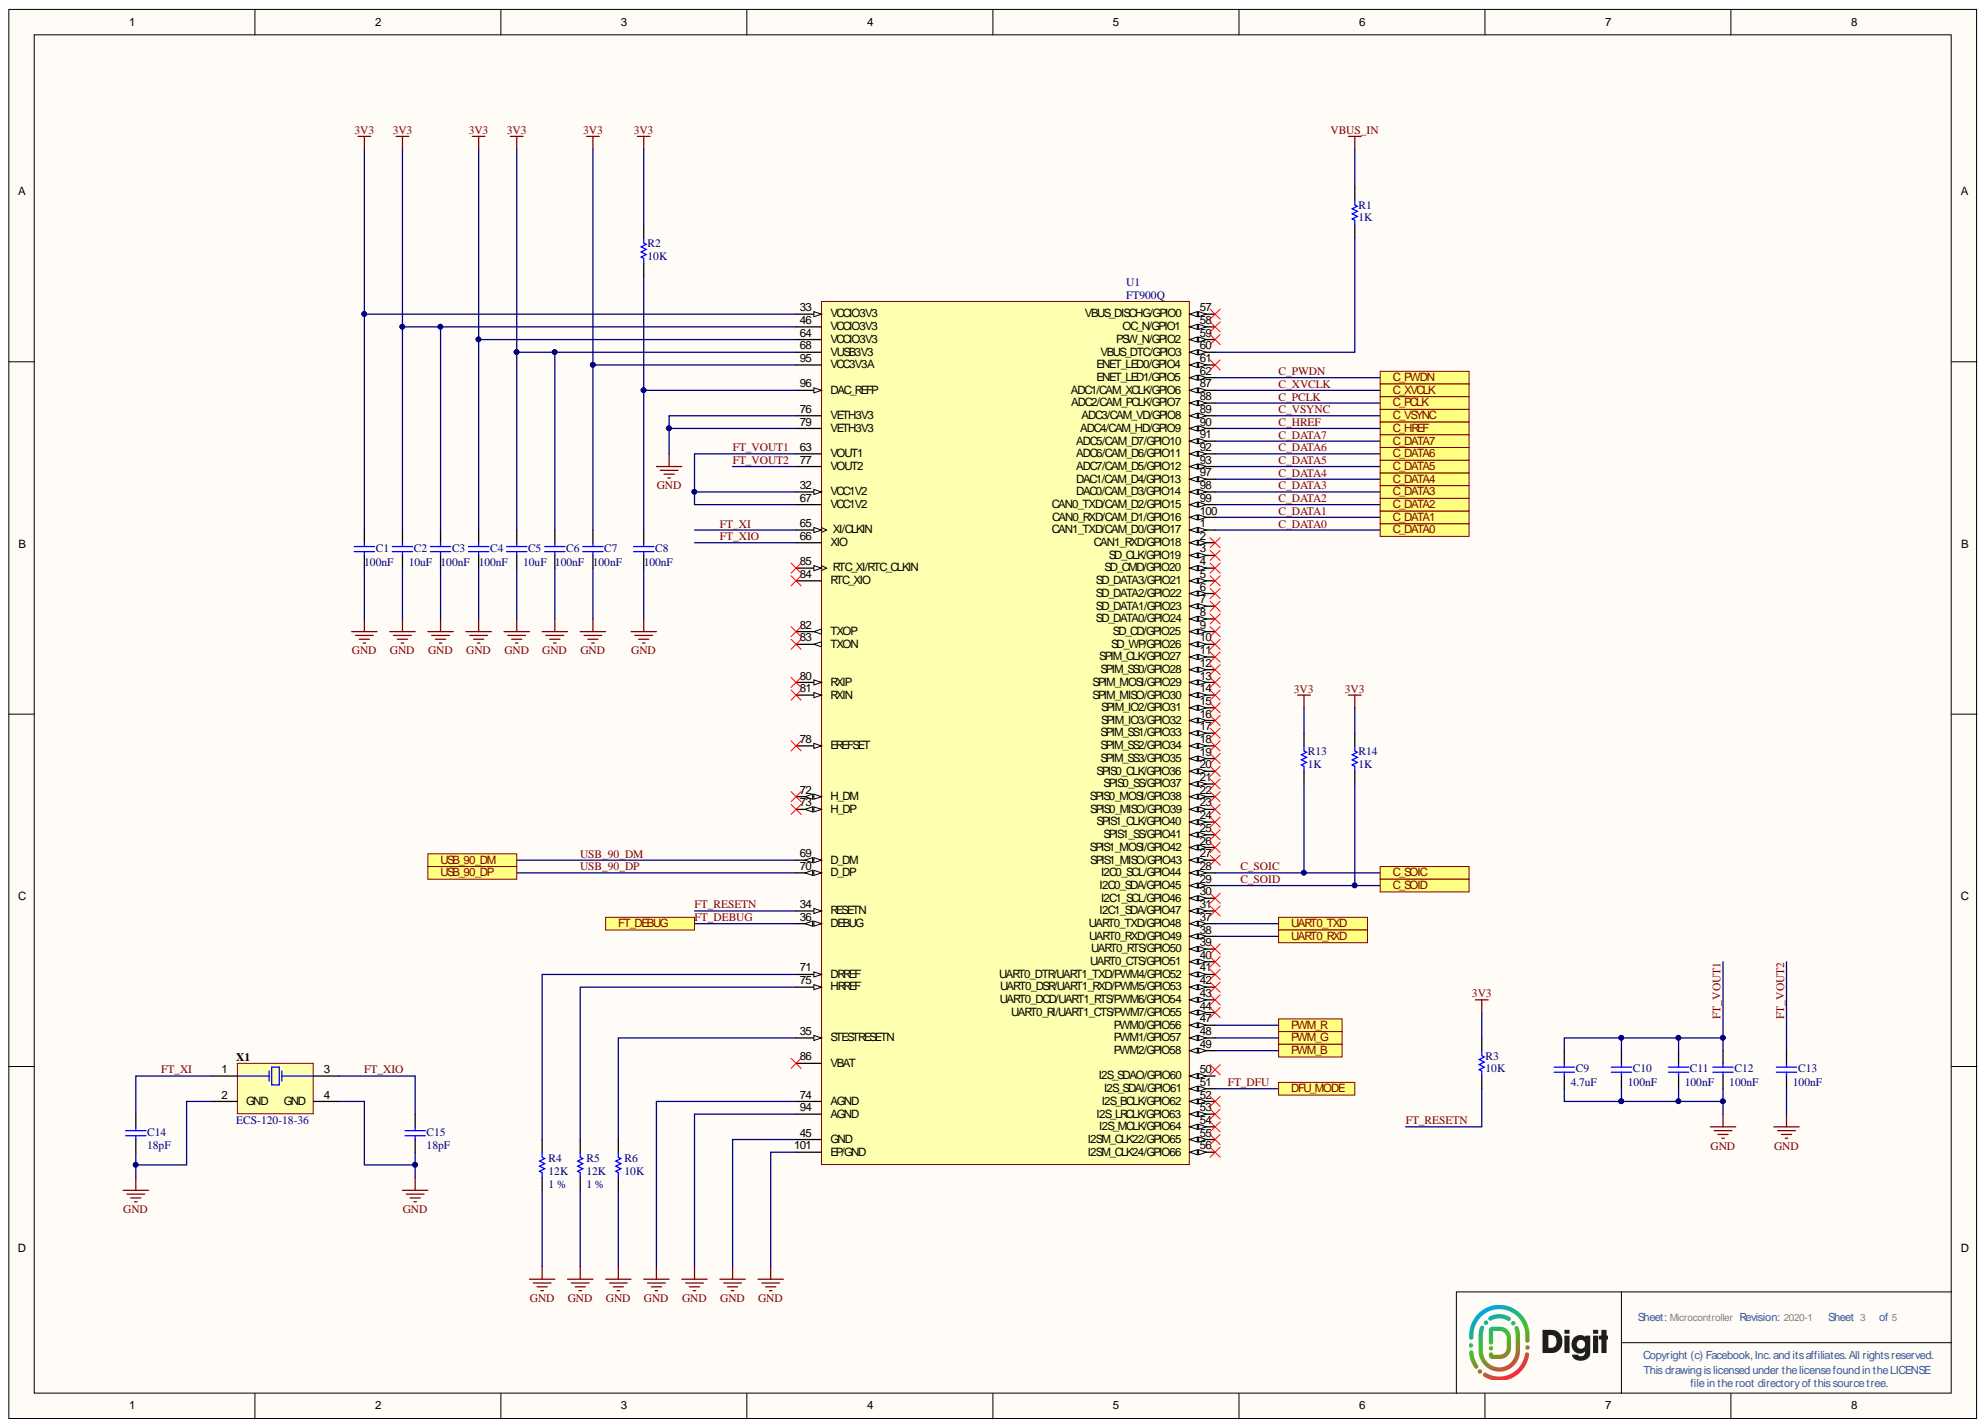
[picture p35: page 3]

4 6 | 5 8
6 4 | 5 9
6 8 | 6 0
9 5
9 6 | | 6 2

8 7 C_X VCLK | C_PW D N

7 6 | | 8 8 C_PCLK

FT_V O UT1 | 6 3 | 9 1 C_D ATA 7

7 9 | 9 0 C_HREF

FT_V O UT2 | 7 7 | 9 3 C_D ATA 5

3 2 | 9 7 C_D ATA 4

USB_9 0_D M | USB_90_D P 7 0 | 2 8
USB_9 0_D P | | 2 9 C_SOID

3 8 | UA RT0_RXD

7 5 | 4 2
3 5 | 4 3

5 2 | FT_RESETN

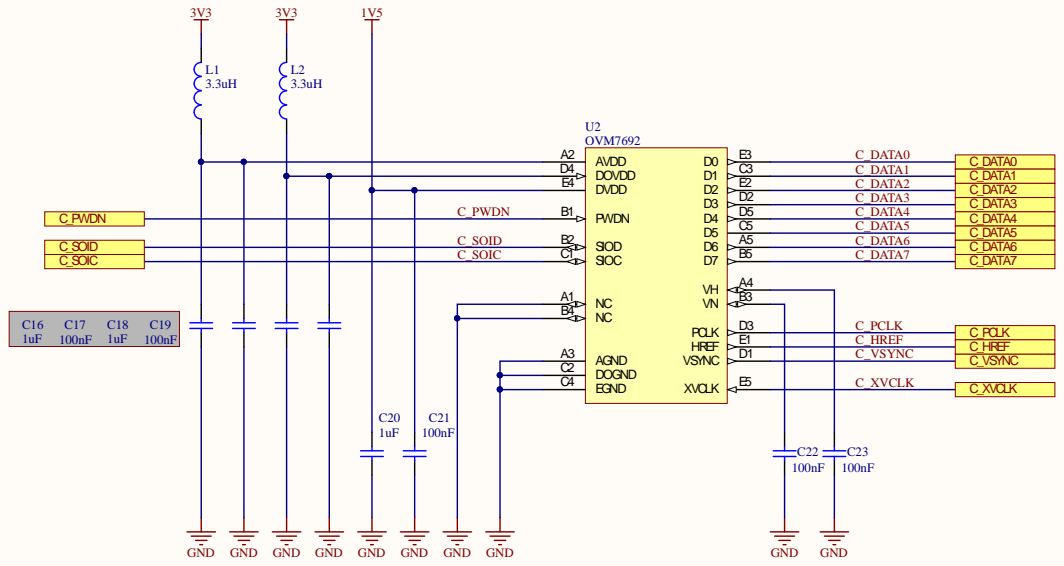
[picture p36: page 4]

D4 | | C3 C_D ATA 1
E4 | | E2 C_D ATA 2

C_PWD N | B 1 | | D2 C_D ATA 3

C_SO I C | C_SOIC | C1 | B5 C_D ATA 7

E1 | | C_HREF
D 1 | | C_VSY N C

C2 | E5
C4

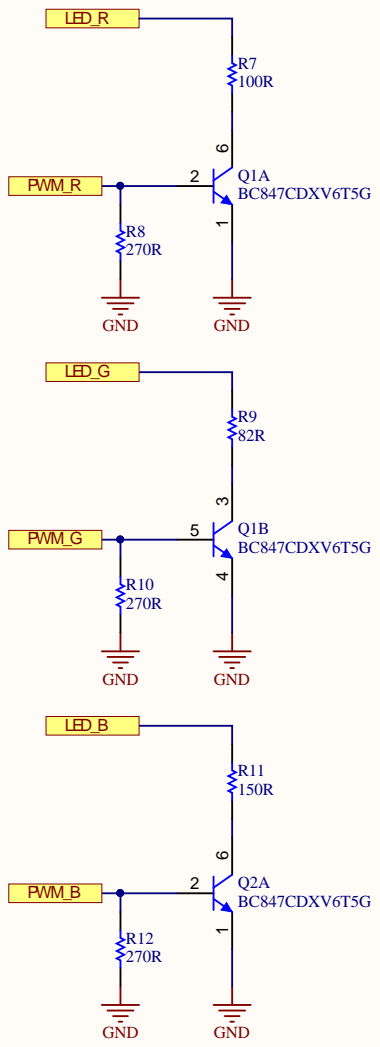
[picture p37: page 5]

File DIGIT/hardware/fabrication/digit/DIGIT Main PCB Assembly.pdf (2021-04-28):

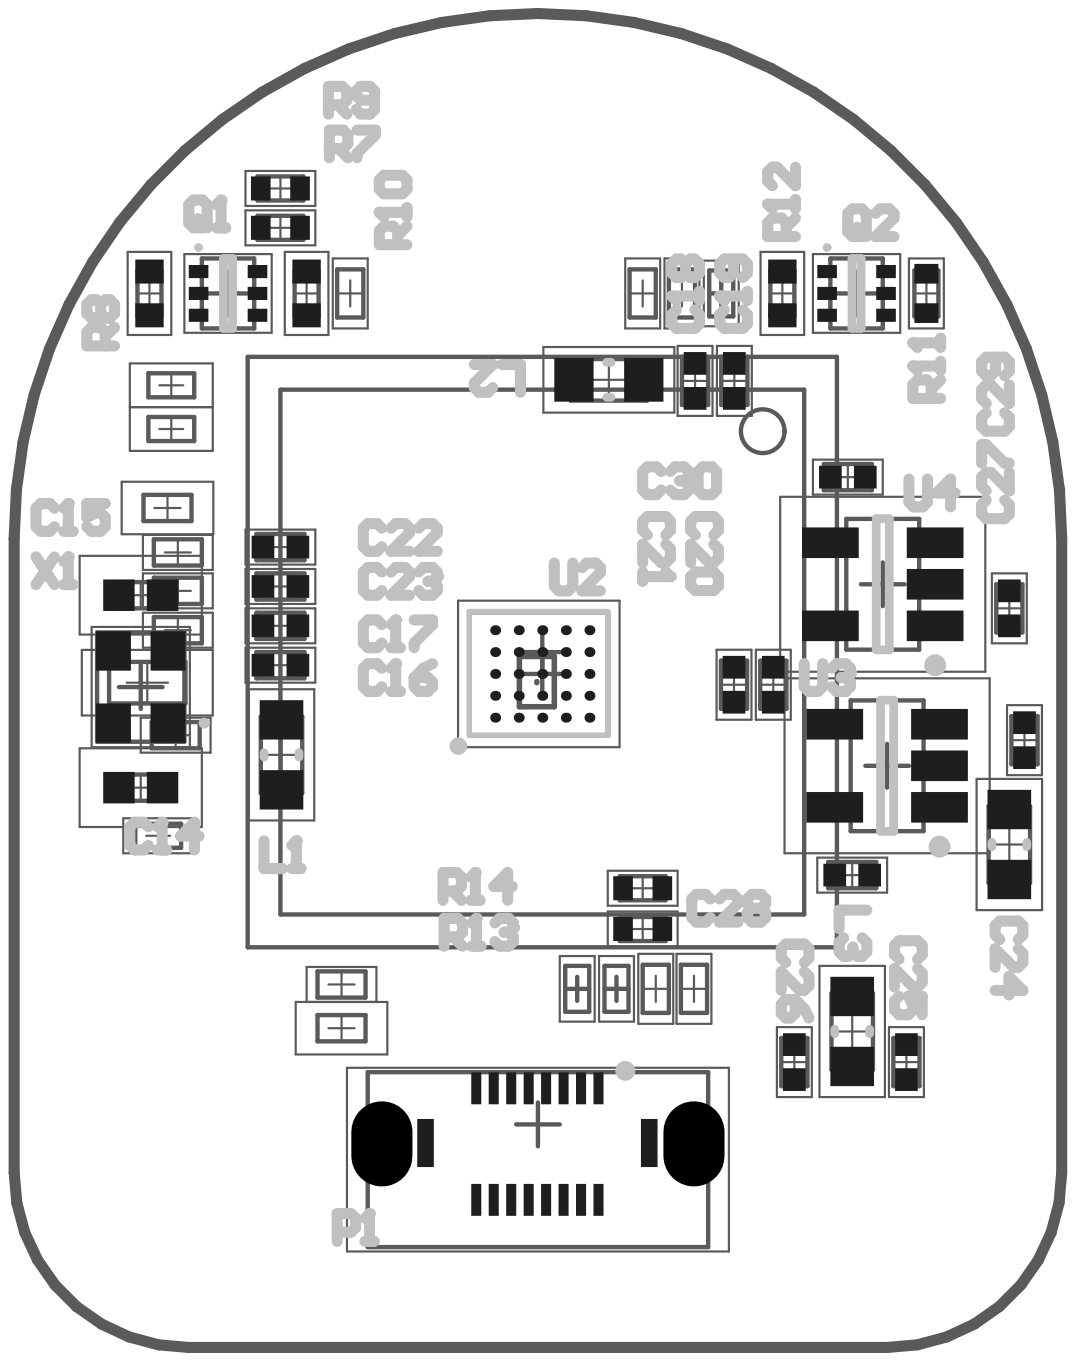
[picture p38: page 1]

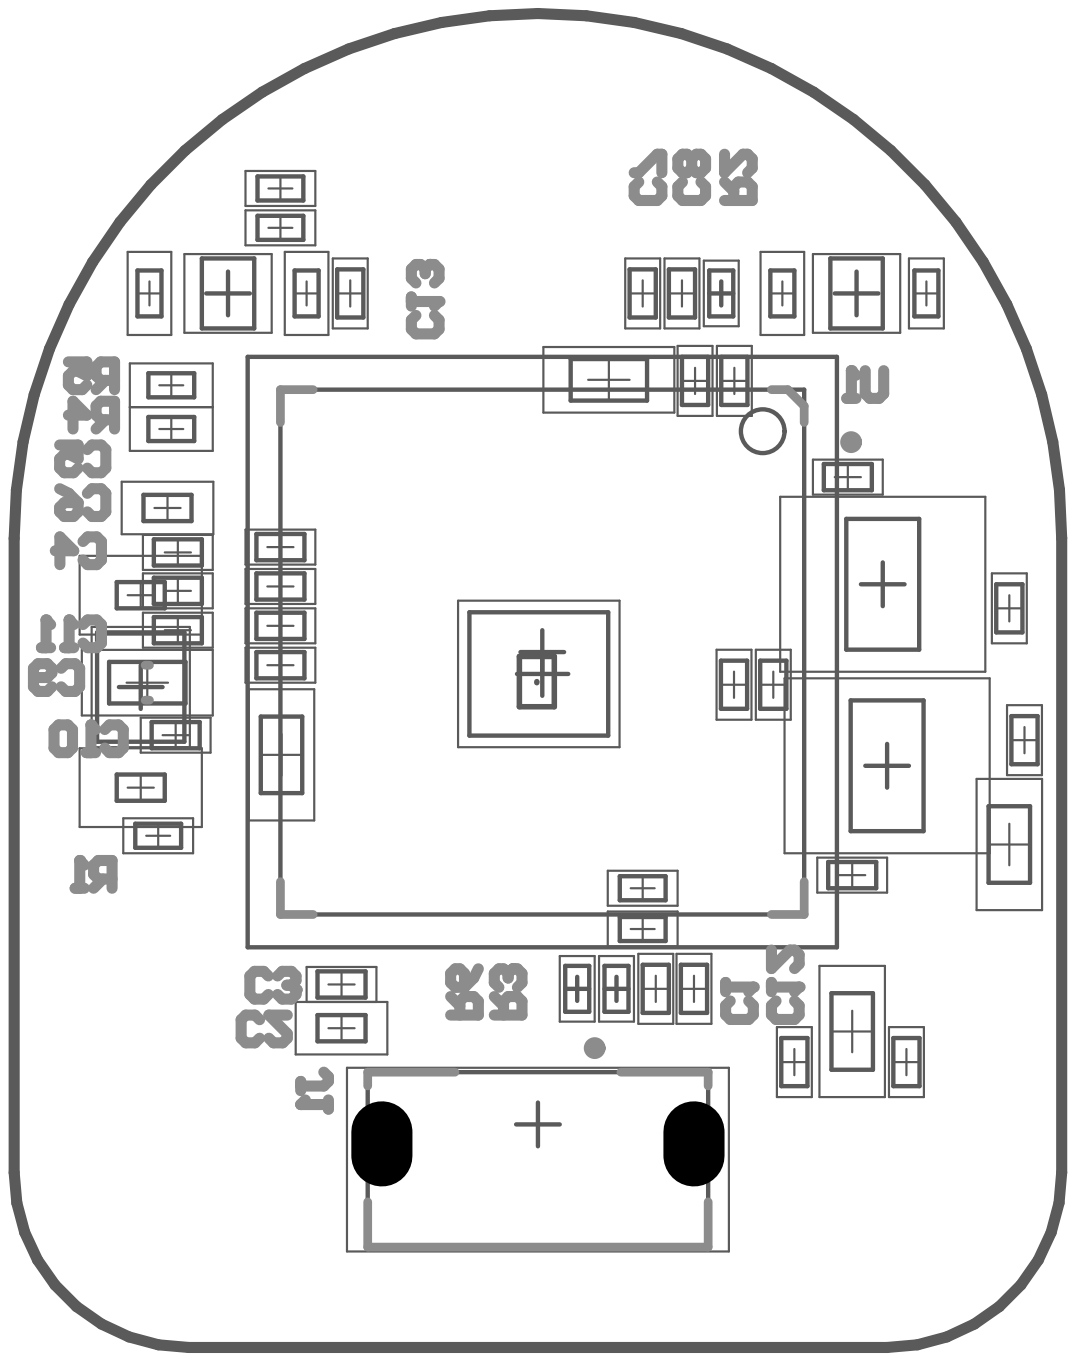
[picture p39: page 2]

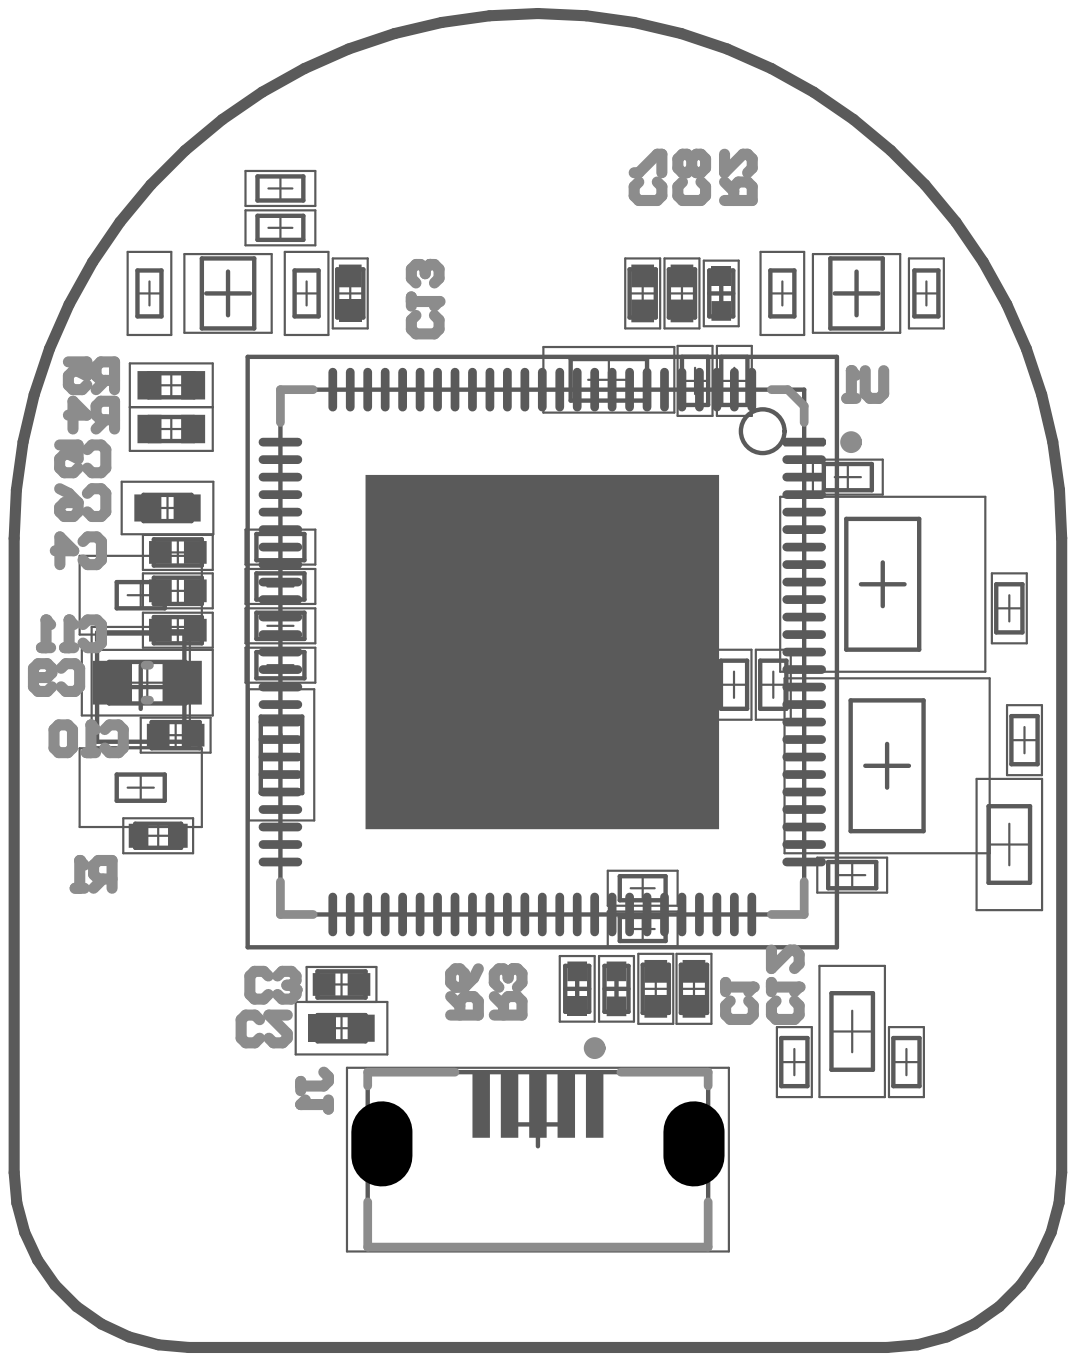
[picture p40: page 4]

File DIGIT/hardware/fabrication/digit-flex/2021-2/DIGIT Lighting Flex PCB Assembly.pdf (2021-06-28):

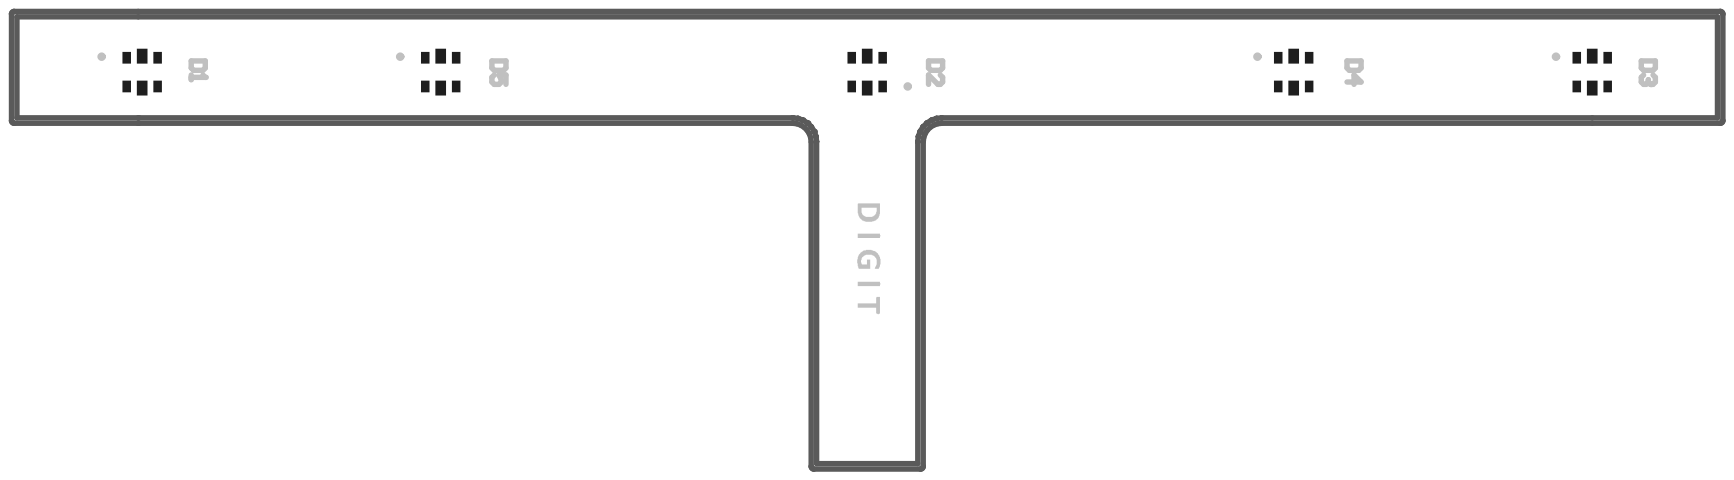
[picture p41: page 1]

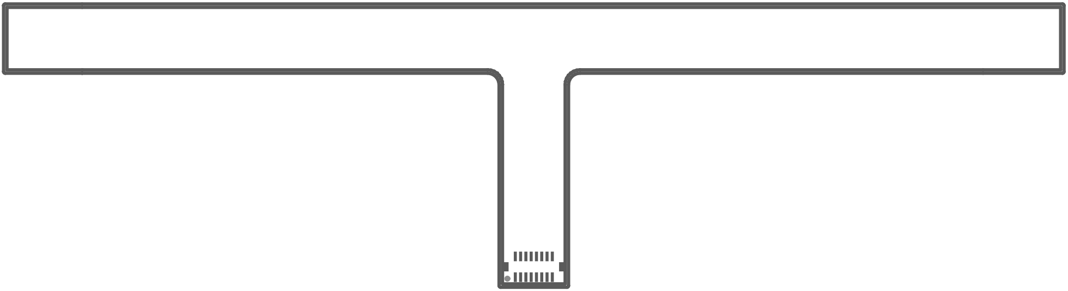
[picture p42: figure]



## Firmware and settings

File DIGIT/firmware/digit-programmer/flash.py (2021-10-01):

# Copyright (c) Facebook, Inc. and its affiliates. All rights reserved.
import os
import sys

import logging
import subprocess

from omegaconf import OmegaConf

from usb.core import find as find_device

DIGIT_SERIAL_MASK = "DXXXXX".encode("utf-16le")
DIGIT_SERIAL_ID_LENGTH = 5
DFU_UTIL_CMD = "dfu-util"
DFU_TMP_BIN = "digit_firmware_tmp.bin"

_log = logging.getLogger("DigitProgrammer")
logging.basicConfig(level=logging.DEBUG)


def format_serial(serial):
    if not serial.isdigit() or len(serial) > DIGIT_SERIAL_ID_LENGTH:
        _log.error("Serial must be between 1 and 5 characters long.")
        sys.exit(1)
    serial = "D{}".format(serial.rjust(DIGIT_SERIAL_ID_LENGTH, "0"))
    serial = serial.encode("utf-16le")
    return serial


def set_serial(firmware_bin, serial):
    _log.info(f"Attempting to find DIGIT serial mask in {firmware_bin} binary.")
    with open(firmware_bin, "rb") as firmware_f:
        firmware_data = firmware_f.read()
    if firmware_data.find(DIGIT_SERIAL_MASK) < 0:
        _log.error("Could not find serial pattern in firmware!")
        sys.exit(1)
    _log.info("Found serial pattern...")
    firmware_data = firmware_data.replace(DIGIT_SERIAL_MASK, serial)
    with open(DFU_TMP_BIN, "w+b") as firmware_tmp:
        firmware_tmp.write(firmware_data)
    _log.info("Serial number written to new firmware binary.")


def find_digit_usb_dev(id_vendor, id_product):
    dev = find_device(idVendor=id_vendor, idProduct=id_product)
    return dev


def reset_device(usb_dev):
    usb_dev.reset()


def program_digit():
    cwd = os.path.dirname(os.path.realpath(__file__))
    dfu_util_args = [DFU_UTIL_CMD, "-vRD", DFU_TMP_BIN]
    subprocess.run(dfu_util_args, cwd=cwd)


def main():
    cli_conf = OmegaConf.from_cli()
    base_conf = OmegaConf.load("programmer.yaml")
    conf = OmegaConf.merge(base_conf, cli_conf)
    _log.info(f"DIGIT programmer config: {conf}")

    full_serial = format_serial(str(conf.digit.serial))
    set_serial(conf.digit.firmware, full_serial)

    _log.info("Flashing DIGIT firmware...")
    input("Unplug and plug DIGIT into usb then press ENTER...")
    program_digit()
    _log.info("Finished flashing firmware to DIGIT!")


if __name__ == "__main__":
    sys.exit(main())

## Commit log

2020-06-01 added adaptor files for DIGIT sensor
    [DIGIT-Allegro-main-V1.stl, DIGIT-Allegro-side-V1.stl, DIGIT-Robotiq Adapter-2F85-V1.STL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]
2020-06-01 renamed adaptors directory
    [DIGIT-Allegro-main-V1.stl, DIGIT-Allegro-side-V1.stl, DIGIT-Robotiq Adapter-2F85-V1.STL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]
2020-06-06 updated manufacturing files for PCBA
    [digit_copper_signal_1.gbr, digit_copper_signal_2.gbr, digit_copper_signal_bot.gbl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]
2020-06-06 updated readme for pcba fab
2020-10-19 Added assembly files and adhesive outline to mechanical layer
2020-10-19 added main pcb assembly file
2020-10-19 updated release package to include assembly views and adhesive information on mechanical layers
2021-06-28 rev 2021-2 for digit flex and addressed part subs
    [digit_flex.gbl, digit_flex.gbo, digit_flex.gbp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]
2021-08-12 latest mechanical enclosure revision
    [Acrylic.STEP, Acrylic_Clip_w_Snap.STEP, Acrylic_Clip_w_Snap.STL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]
2021-10-01 Master (#29)
    * prevent digit serials longer than 5 characters
    [flash.py]
2024-03-11 Add DIGIT Pinki files and refactor folder structure (#41)
    [Acrylic_Final.DXF, Acrylic_Final.STEP, AllegroHandAdaptor_3Fibers.step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]

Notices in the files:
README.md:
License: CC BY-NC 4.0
